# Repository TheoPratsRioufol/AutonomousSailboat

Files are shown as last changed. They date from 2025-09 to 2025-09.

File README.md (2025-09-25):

# An Autonomous Sailboat To Cross the Ocean

This GitHub repository presents the engineering of *Posidonie*, a 2-meter sailboat designed to compete in the [Microtransat challenge](https://www.microtransat.org/), which involves crossing the Atlantic Ocean autonomously.

plot
**Fig 1:** The CAD Model of the *Posidonie* monohull autonomous sailboat.

The Journey started with a 1.3-meter prototype, *Baleine*, from an RC M Class sailboat:

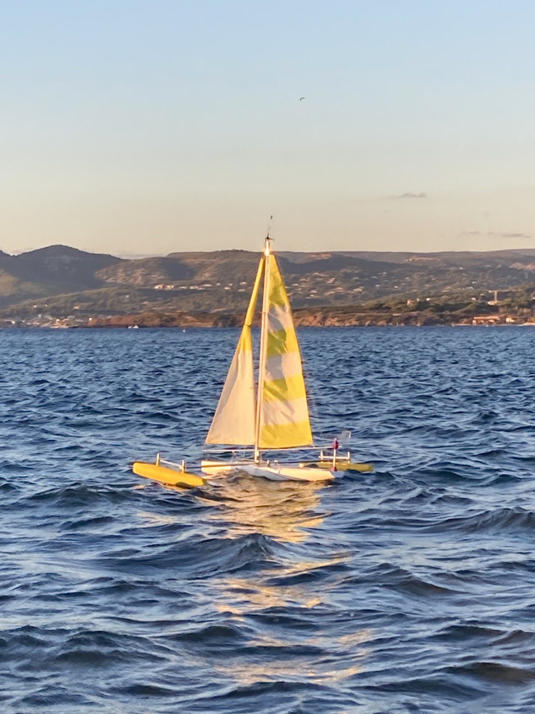
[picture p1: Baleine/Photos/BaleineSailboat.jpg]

**Fig 2:** The *Baleine* saiboat in a upwind course. You may notice the purple windvane at the back. The sail is controlled thanks to an electric winch.

This boat was used to test the control law, the fiberglassing process for the hull, and the architecture of the embedded electronics. 

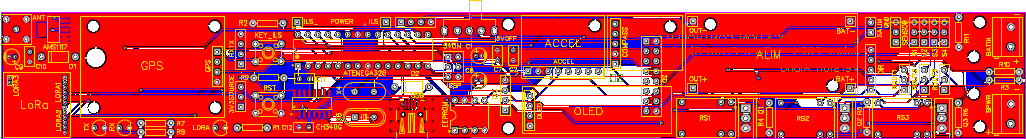
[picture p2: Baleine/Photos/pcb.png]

**Fig 3:** The *Baleine* main PCB. A LoRa module is used to communicate with a ground station. A GPS module and a magnetic compass provide the 6D position of the sailboat.

The promising results validated the global architecture. Meanwhile, the lack of upwind sailing performance ensured the need for a more precise design of the drift and sail area. This sizing is usually performed by a *Velocity Prediction Program* (VPP) program. As an open source VPP for this design was not available, a custom one has been developed:

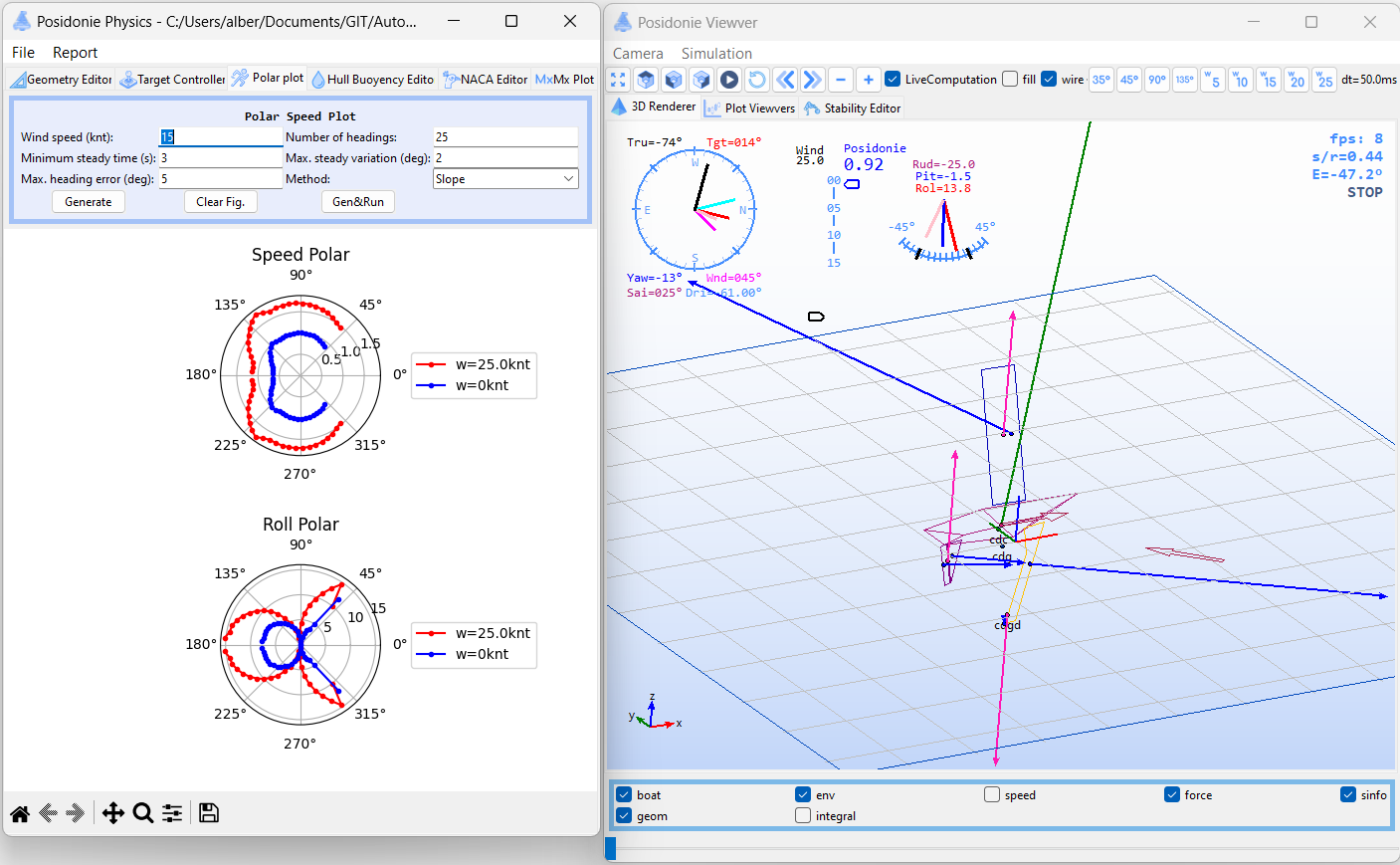
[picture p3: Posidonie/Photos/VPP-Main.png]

**Fig 4:** The *Velocity Prediction Program*. From CFD simulations of the Hull, Drift, and Rudder drag and lift, and according to the sail's control law and sail efficiency, different metrics of the sailboat are computed. (Here the polar plot - i.e., the velocity of the boat for different wind incidence)

The VPP program is fed from CDF Simulation of a NACA Profile under turbulent flow (for the drift, sail, and rudder) using COMSOL, and a hull drag profile in a free surface flow (Ansys Fluent).

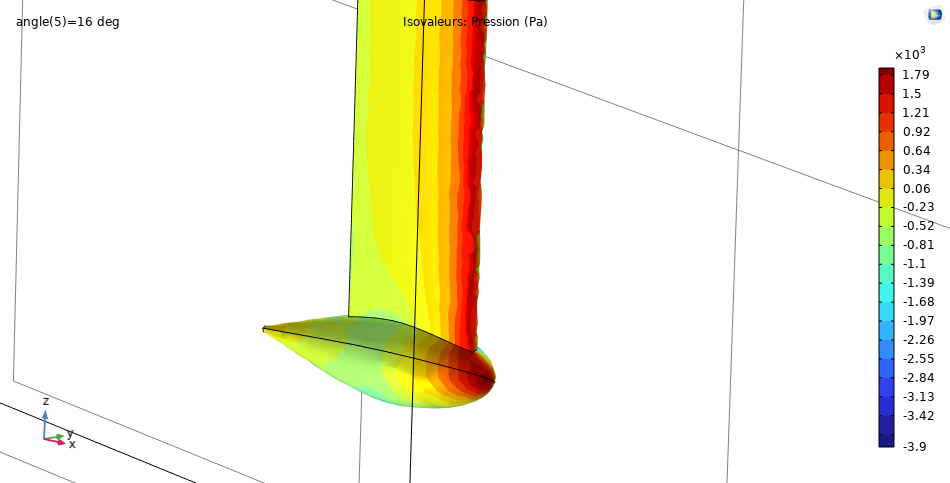
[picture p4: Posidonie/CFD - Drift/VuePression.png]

**Fig 5:** CFD Simulation of the keel's drag and lift as a function of the drift angle (usually around 4°).

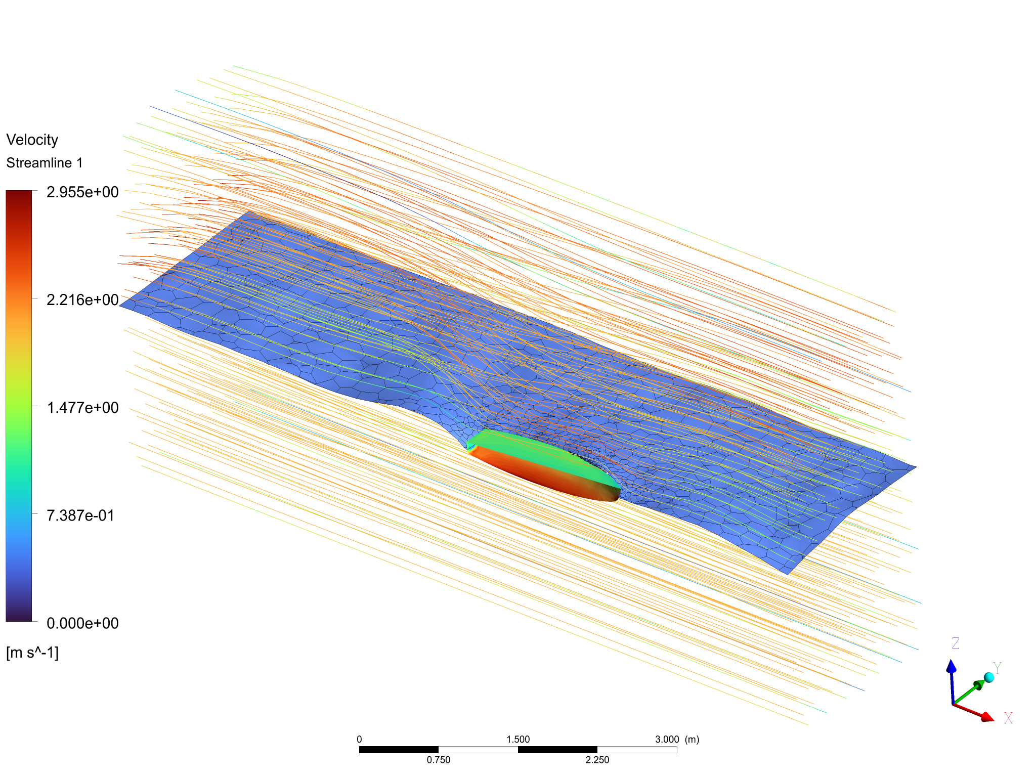
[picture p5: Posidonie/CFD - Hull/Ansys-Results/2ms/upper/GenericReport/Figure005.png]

**Fig 6:** CFD Simulation of the hull drag. As it is a displacement hull, the wave induced by the boat accounts for more than 60% of the overall drag.

To tackle the effect of waves on rotation movements and loads, a hydrodynamic refraction analysis was performed in Ansys AQWA. Past Weather forecast from the [Copernicus](https://www.copernicus.eu/fr) European model has been used in five typical zones (see Fig.7) to produce a statistical model of the wave's period and amplitude. The response of the hull for the most critical wave gave the location of the main beam of the boat's structure, located in the highest stress point (see Fig.8)

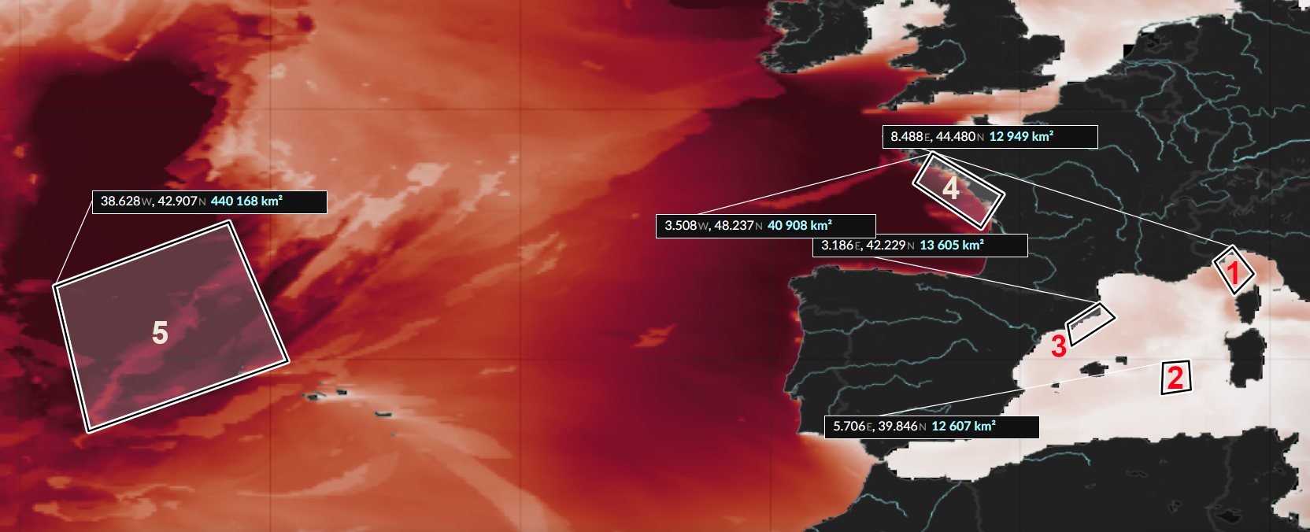
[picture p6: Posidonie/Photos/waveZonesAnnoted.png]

**Fig 7:** Zone considered to build a wave model. It turned out that all the waves created by the wind have similar characteristics. Only the swell greatly varies from each zone.

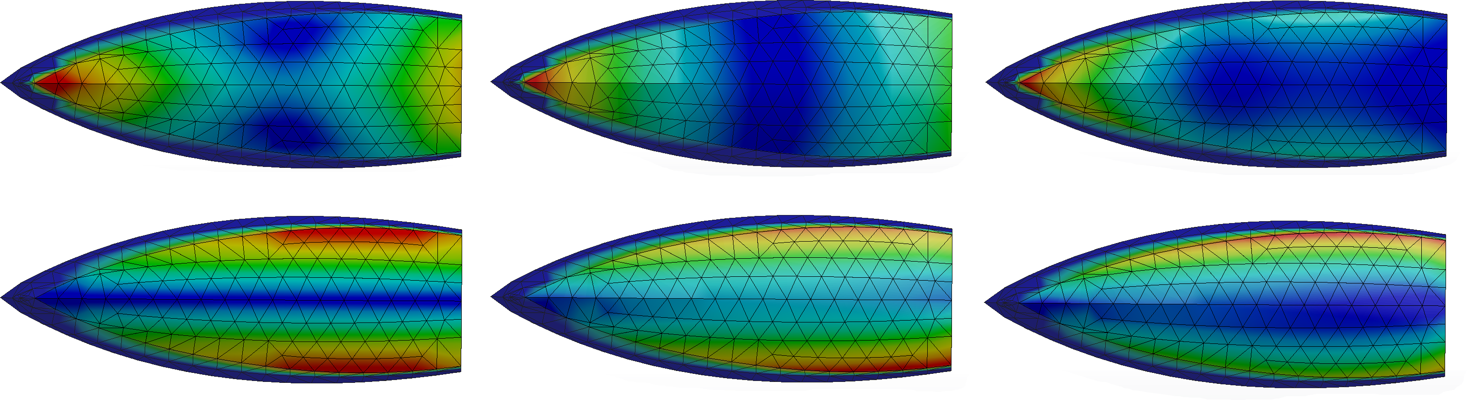
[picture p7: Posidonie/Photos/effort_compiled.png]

**Fig 8:** Location of the wave-hull mains pressure point, for the roll and pitch resonating frequency.

From the results of this main design step (sail surface, keel weight, and length...), a CAD model has been proposed (see Fig 1.). The physical implementation uses plywood and fiberglass as the main material. Prelemeray test of the plywood - fiberglass bound ensures a good mechanical strength of the boat:

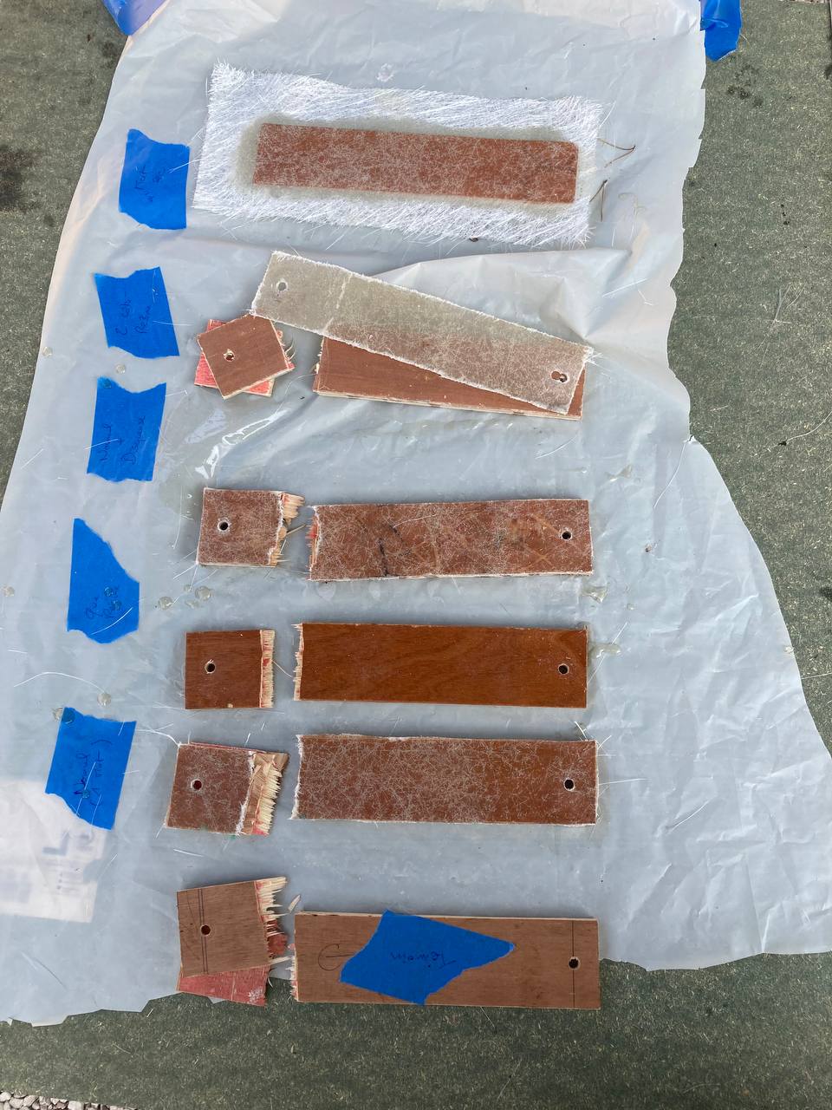
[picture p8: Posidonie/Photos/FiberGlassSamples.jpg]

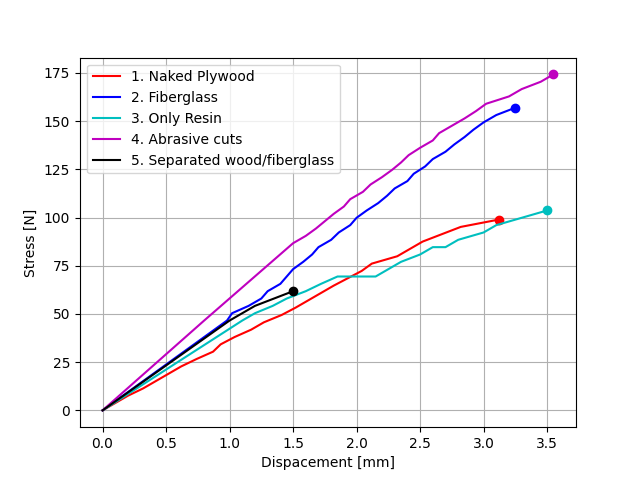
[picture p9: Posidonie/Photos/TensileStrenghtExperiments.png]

**Fig 9:** Sample of plywood-fiberglass composite for a strength analysis.

After countless hours, the hull is finally done!

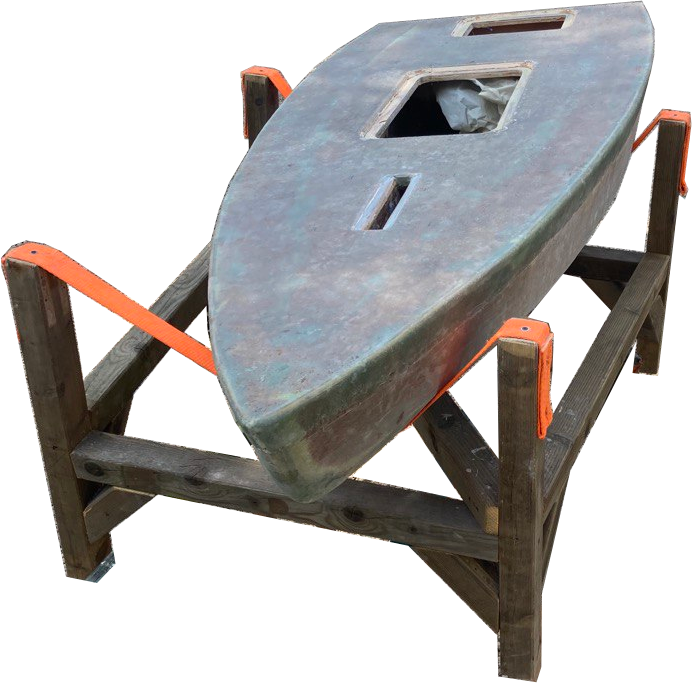
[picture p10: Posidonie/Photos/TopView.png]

**Fig 10:** The physicall hull before the Epoxy coating

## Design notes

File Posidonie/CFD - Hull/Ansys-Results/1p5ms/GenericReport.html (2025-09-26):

ANSYS Logo

Title

Generic Report

Date

2025/05/14 23:08:41

# Contents

Figure 1 Iso View of Wireframe
Figure 2 Iso View of Wireframe
Figure 3 Iso View of Wireframe
Figure 4 Iso View of Wireframe
Figure 5 Iso View of Wireframe
Figure 6 Iso View of Wireframe
Figure 7 Iso View of Wireframe
Figure 8 Iso View of Wireframe
1. User Data

Figure 1. Iso View of Wireframe

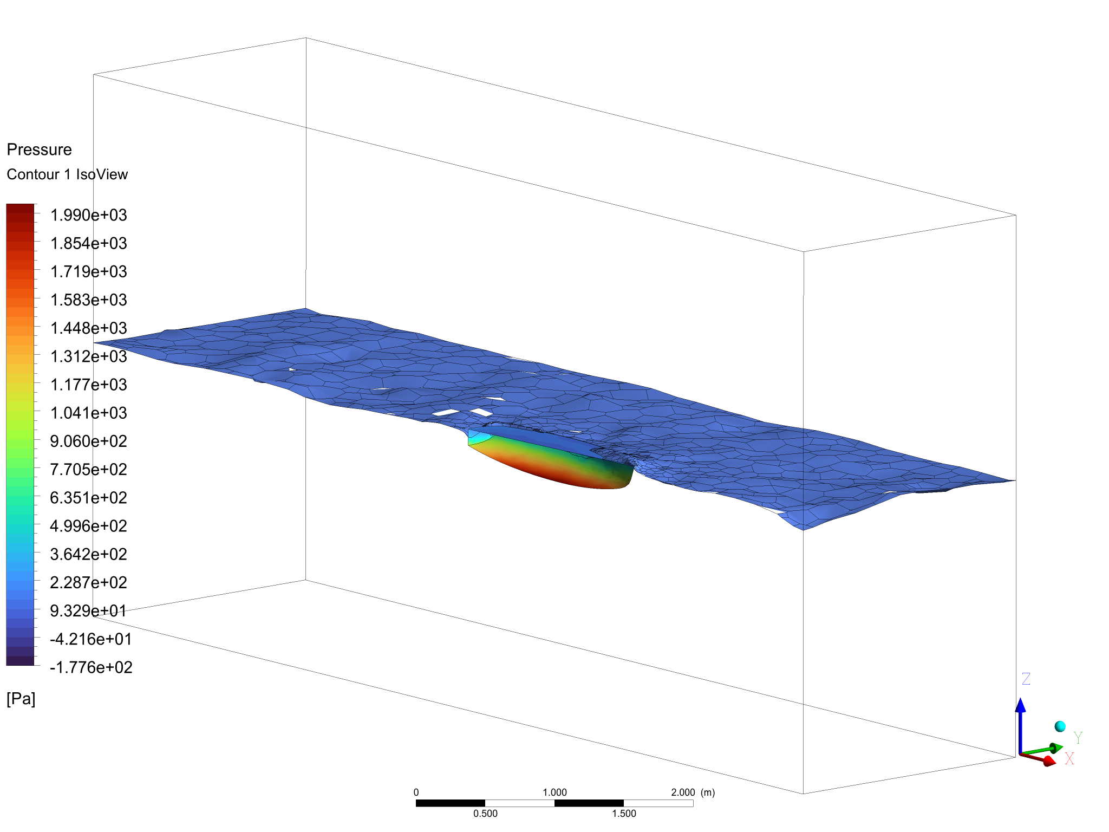
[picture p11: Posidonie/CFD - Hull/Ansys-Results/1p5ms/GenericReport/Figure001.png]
Figure 1 - GenericReport/Figure001.png


Figure 2. Iso View of Wireframe

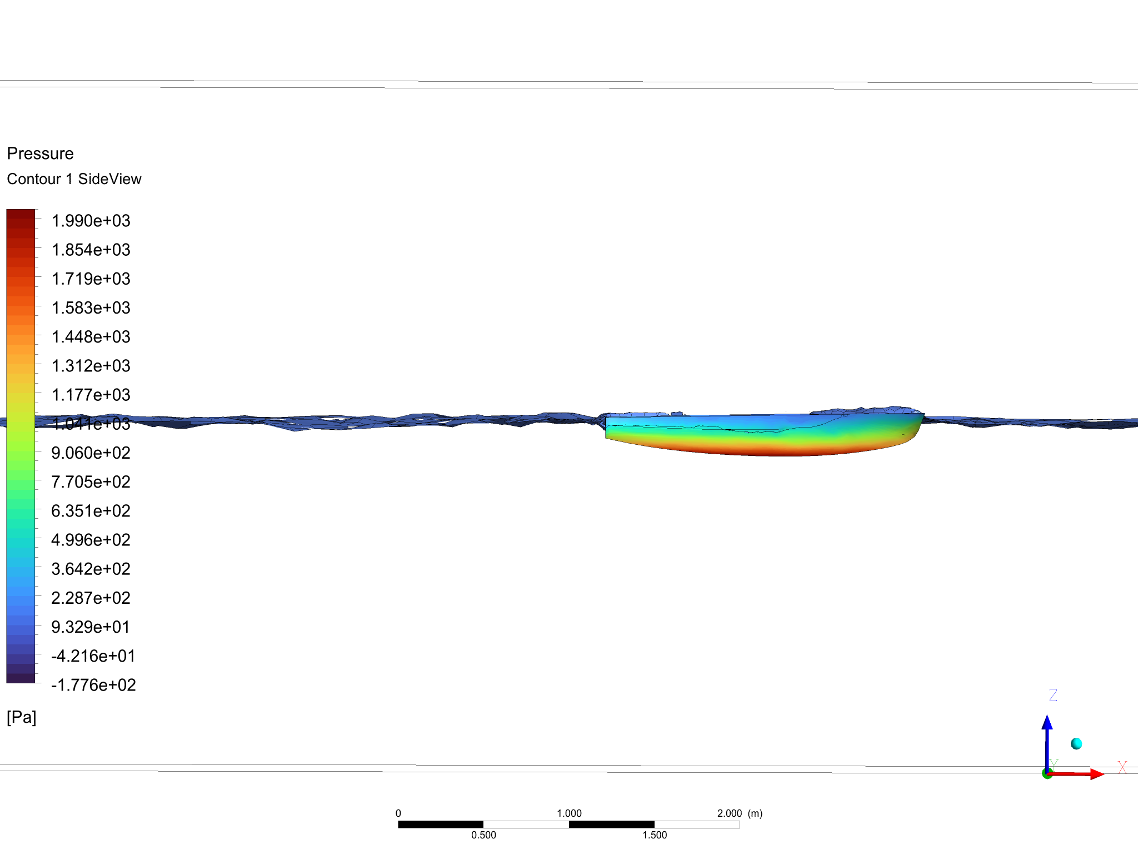
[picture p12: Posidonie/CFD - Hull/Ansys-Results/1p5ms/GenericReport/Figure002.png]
Figure 2 - GenericReport/Figure002.png


Figure 3. Iso View of Wireframe

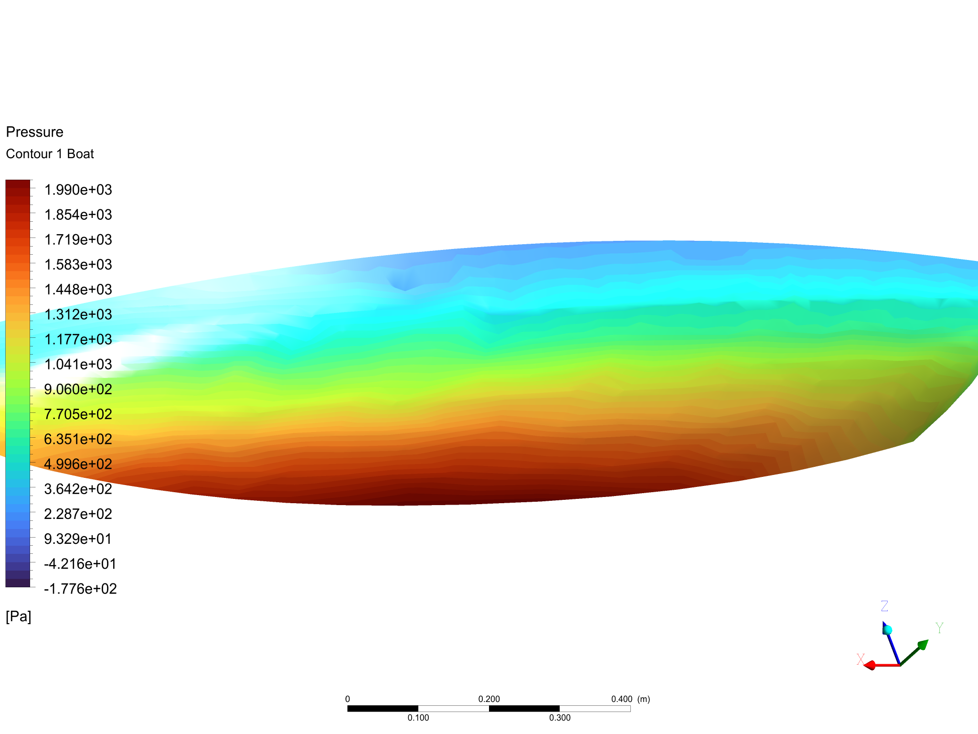
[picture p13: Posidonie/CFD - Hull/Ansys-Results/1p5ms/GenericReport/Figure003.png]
Figure 3 - GenericReport/Figure003.png


Figure 4. Iso View of Wireframe

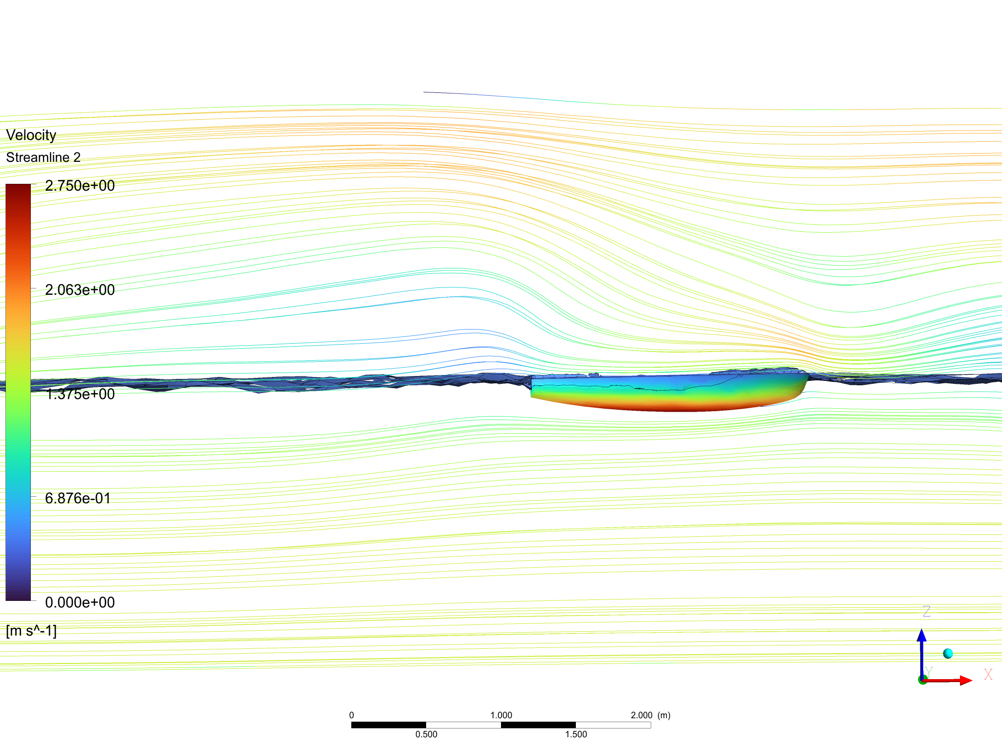
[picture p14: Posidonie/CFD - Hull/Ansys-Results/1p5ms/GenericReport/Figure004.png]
Figure 4 - GenericReport/Figure004.png


Figure 5. Iso View of Wireframe

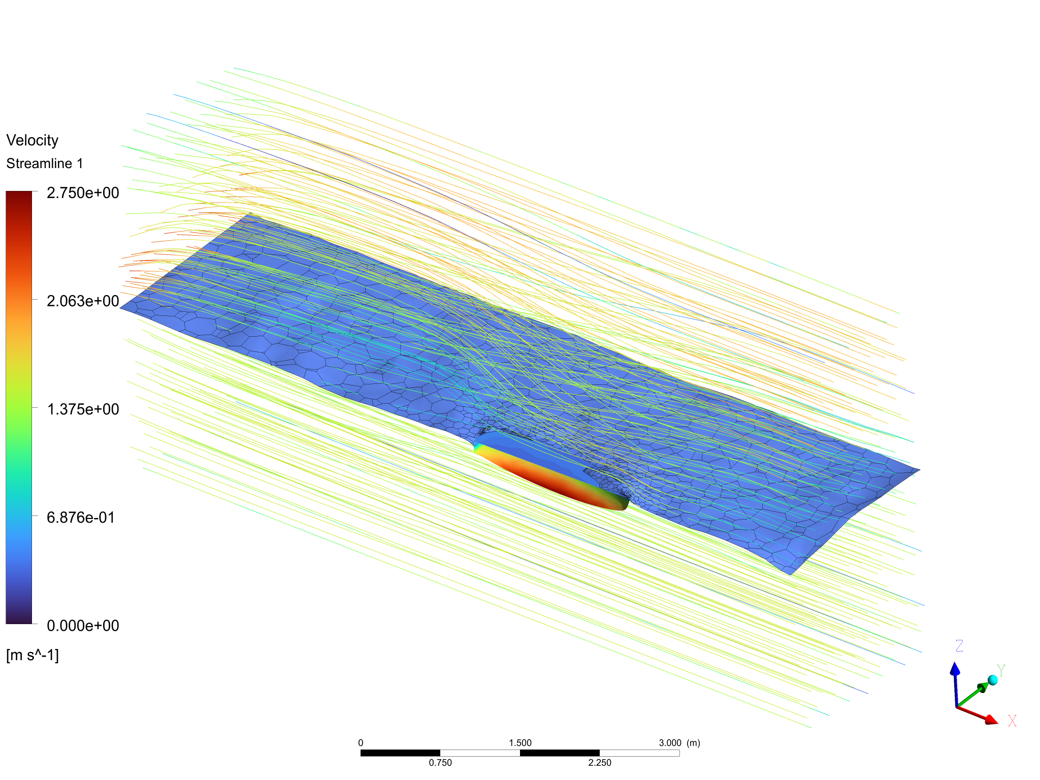
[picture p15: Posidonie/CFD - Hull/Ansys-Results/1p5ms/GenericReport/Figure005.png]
Figure 5 - GenericReport/Figure005.png


Figure 6. Iso View of Wireframe

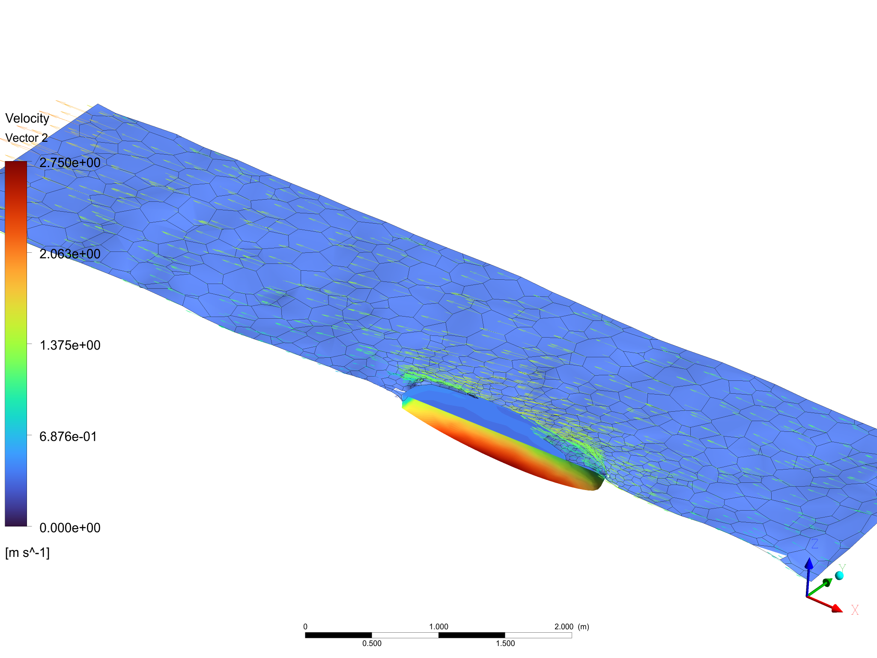
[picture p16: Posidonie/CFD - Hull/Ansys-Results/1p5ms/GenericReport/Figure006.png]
Figure 6 - GenericReport/Figure006.png


Figure 7. Iso View of Wireframe

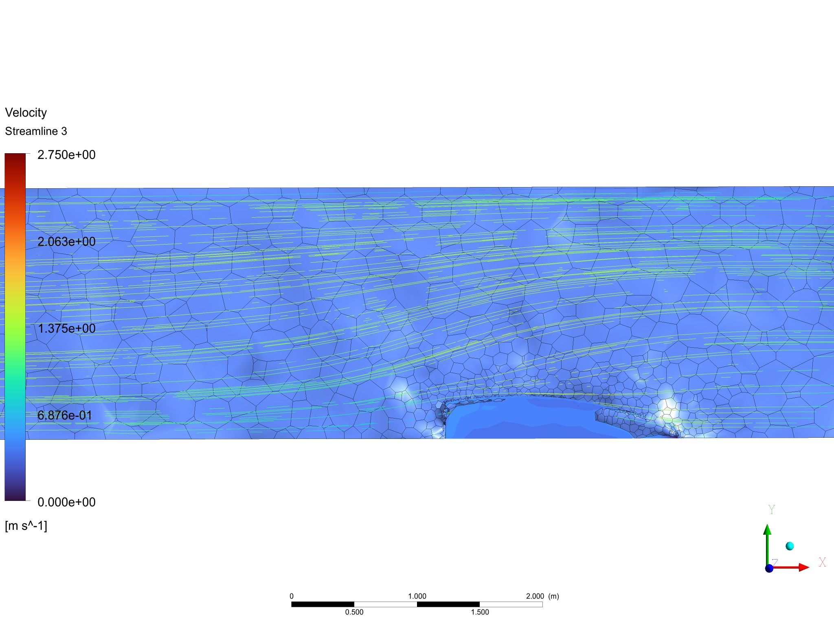
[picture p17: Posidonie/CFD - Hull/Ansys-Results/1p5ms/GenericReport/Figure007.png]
Figure 7 - GenericReport/Figure007.png


Figure 8. Iso View of Wireframe

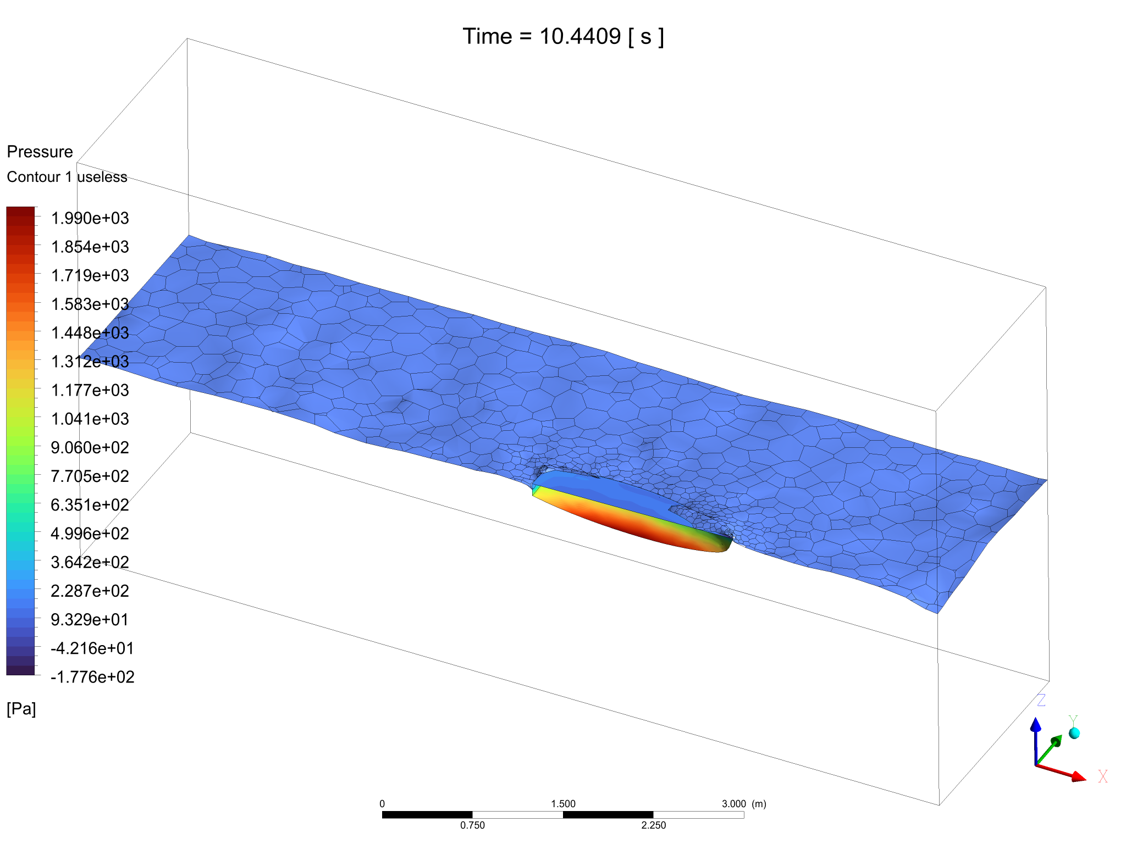
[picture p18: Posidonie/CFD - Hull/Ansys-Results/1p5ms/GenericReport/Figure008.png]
Figure 8 - GenericReport/Figure008.png


# 1. User Data

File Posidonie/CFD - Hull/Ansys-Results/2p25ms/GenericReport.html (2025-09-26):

ANSYS Logo

Title

Generic Report

Date

2025/05/15 01:05:22

# Contents

Figure 1 Iso View of Wireframe
Figure 2 Iso View of Wireframe
Figure 3 Iso View of Wireframe
Figure 4 Iso View of Wireframe
Figure 5 Iso View of Wireframe
Figure 6 Iso View of Wireframe
Figure 7 Iso View of Wireframe
Figure 8 Iso View of Wireframe
1. User Data

Figure 1. Iso View of Wireframe

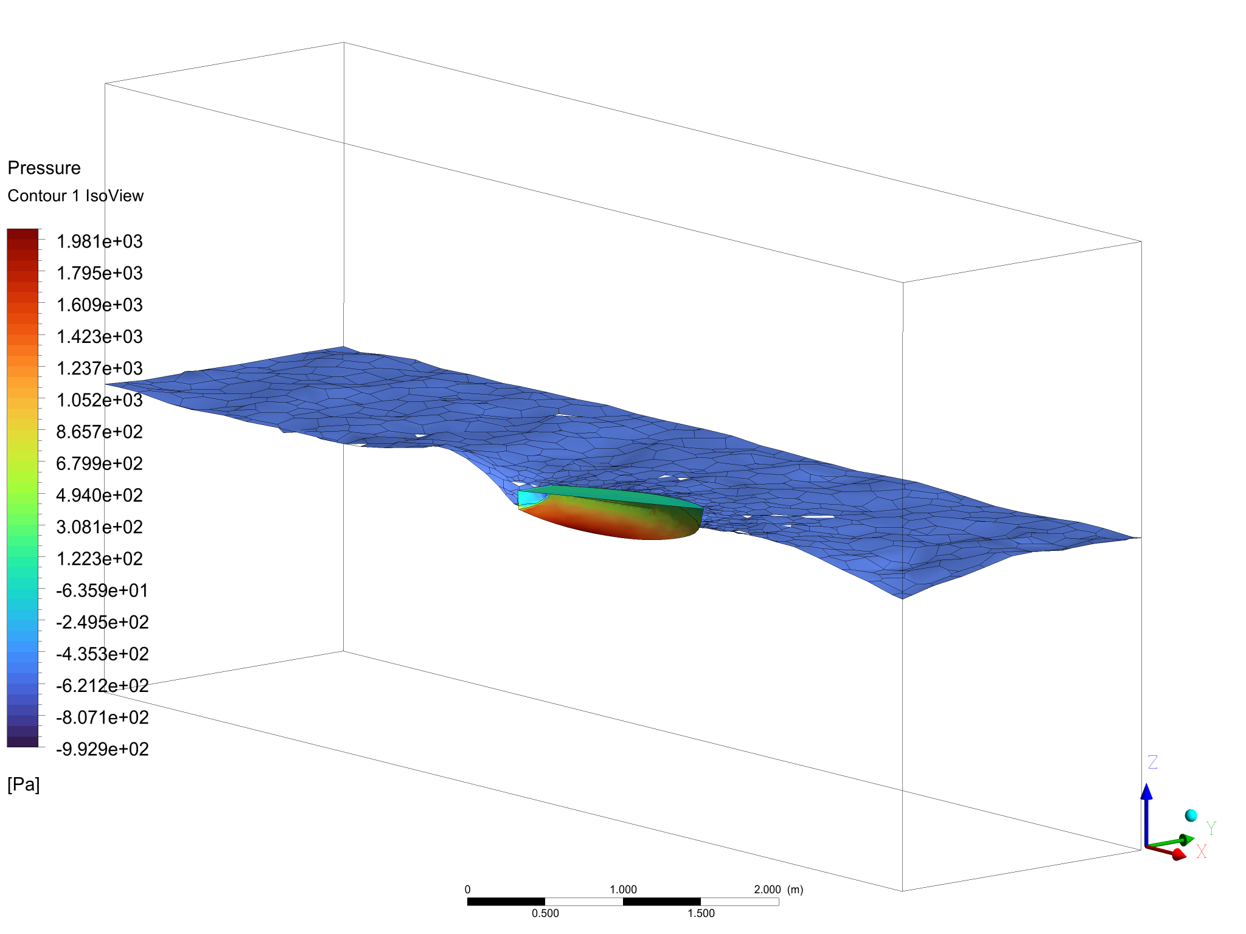
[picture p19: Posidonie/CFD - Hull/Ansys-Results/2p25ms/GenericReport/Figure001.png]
Figure 1 - GenericReport/Figure001.png


Figure 2. Iso View of Wireframe

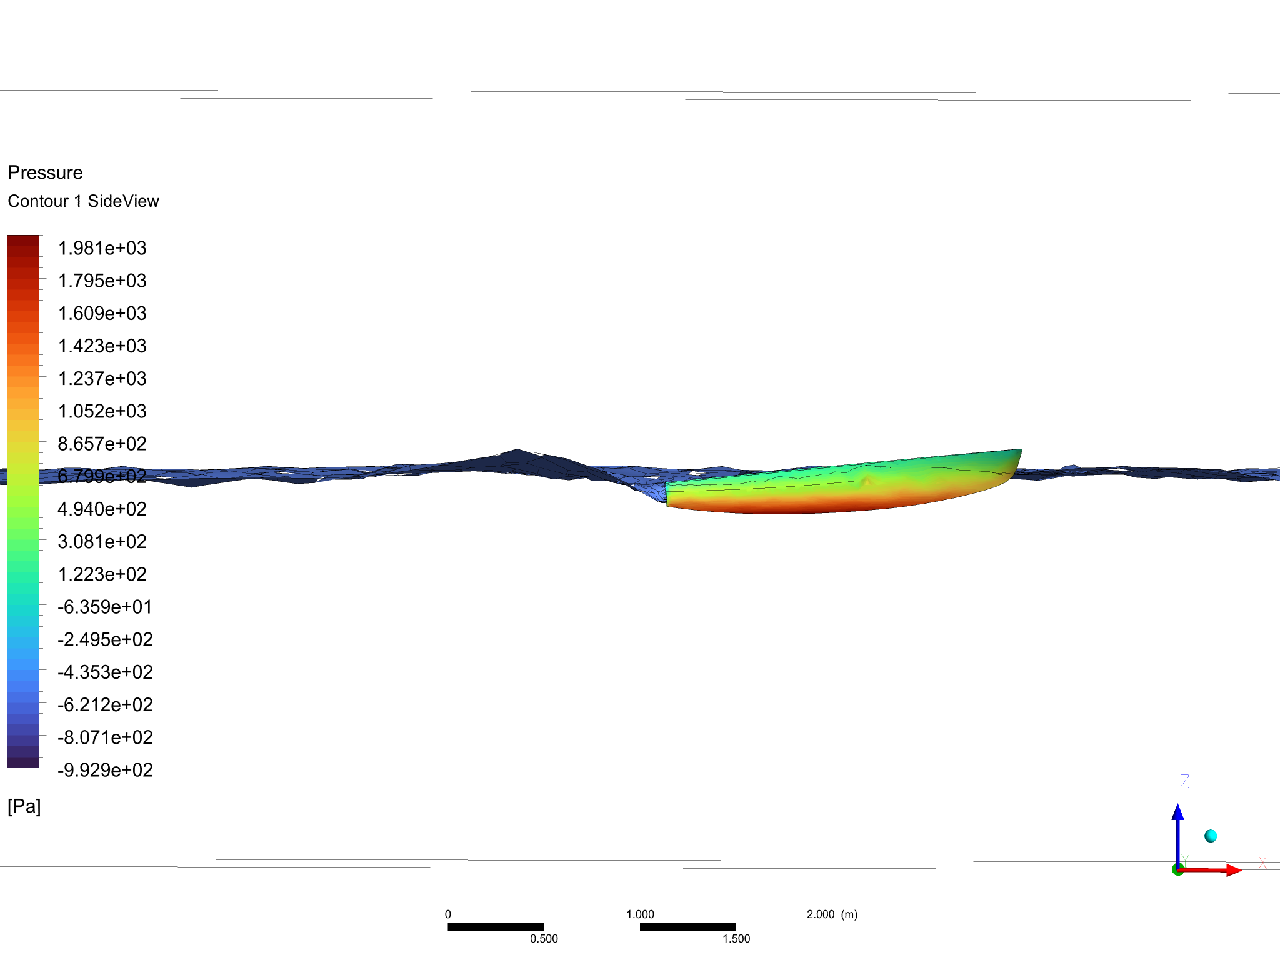
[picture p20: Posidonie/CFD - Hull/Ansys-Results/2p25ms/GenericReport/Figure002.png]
Figure 2 - GenericReport/Figure002.png


Figure 3. Iso View of Wireframe

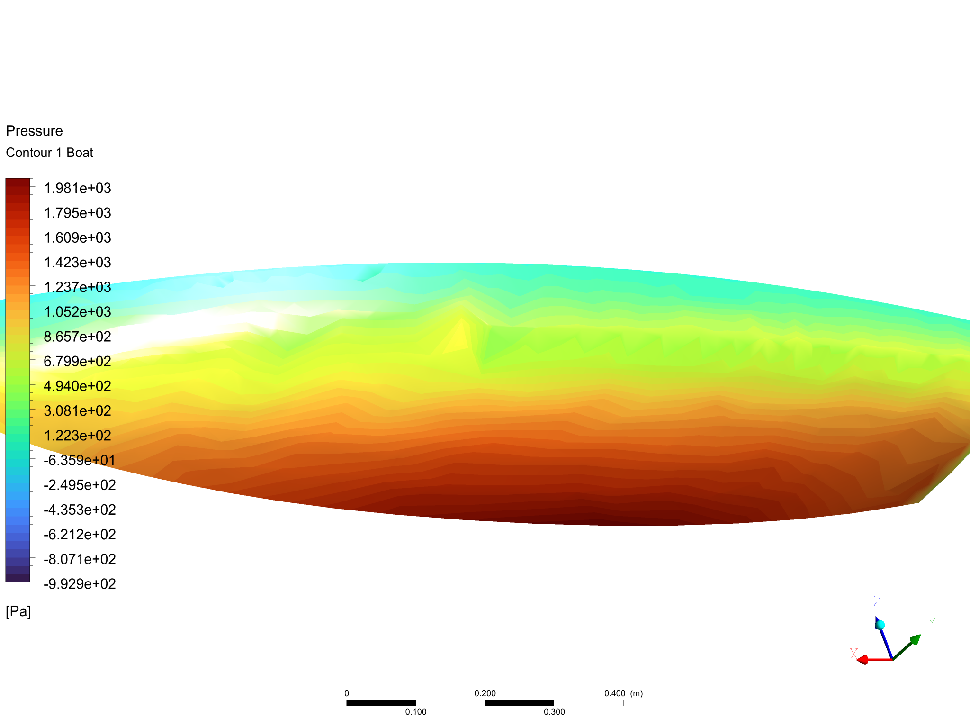
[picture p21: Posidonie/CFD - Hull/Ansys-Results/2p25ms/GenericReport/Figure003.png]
Figure 3 - GenericReport/Figure003.png


Figure 4. Iso View of Wireframe

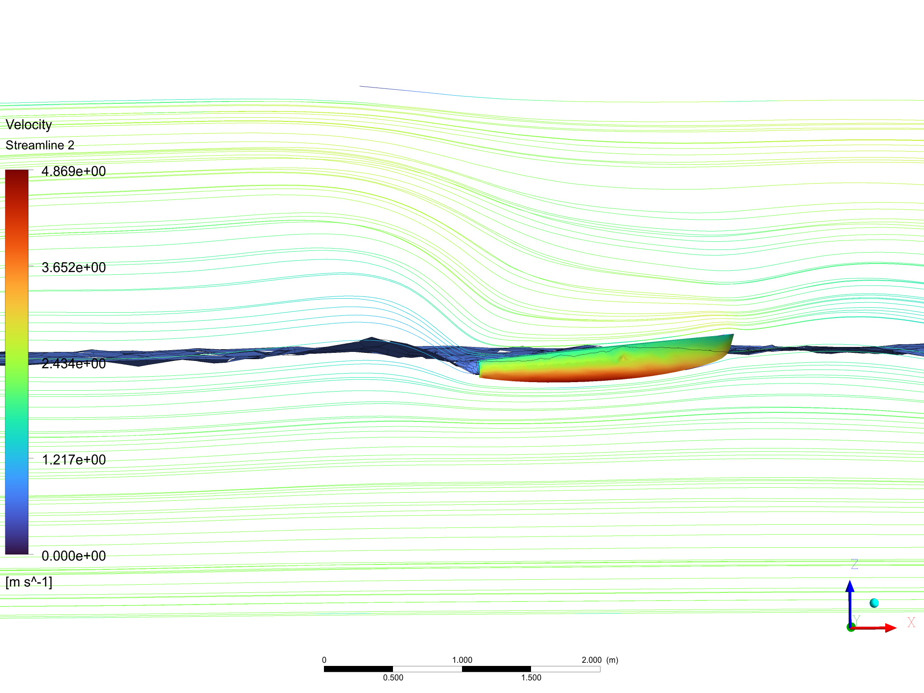
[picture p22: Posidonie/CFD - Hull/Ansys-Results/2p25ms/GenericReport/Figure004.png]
Figure 4 - GenericReport/Figure004.png


Figure 5. Iso View of Wireframe

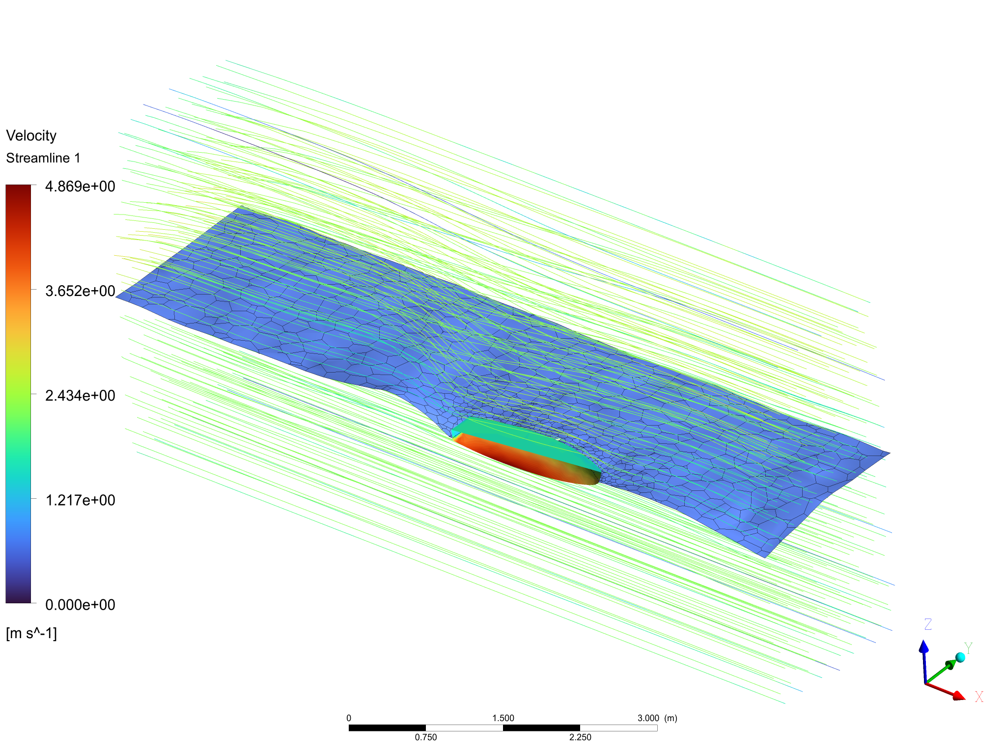
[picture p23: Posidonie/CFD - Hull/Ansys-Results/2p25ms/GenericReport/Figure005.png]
Figure 5 - GenericReport/Figure005.png


Figure 6. Iso View of Wireframe

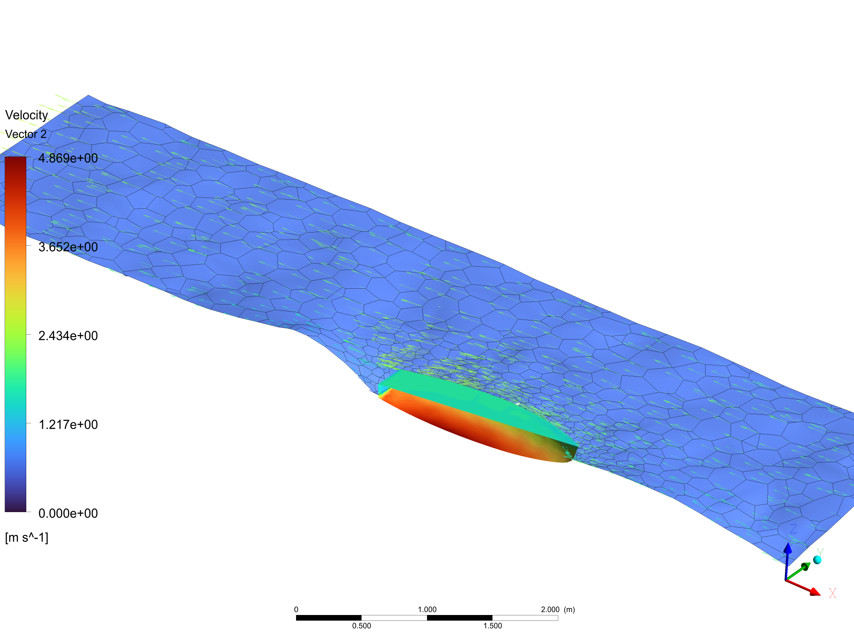
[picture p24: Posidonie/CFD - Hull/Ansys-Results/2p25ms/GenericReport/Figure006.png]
Figure 6 - GenericReport/Figure006.png


Figure 7. Iso View of Wireframe

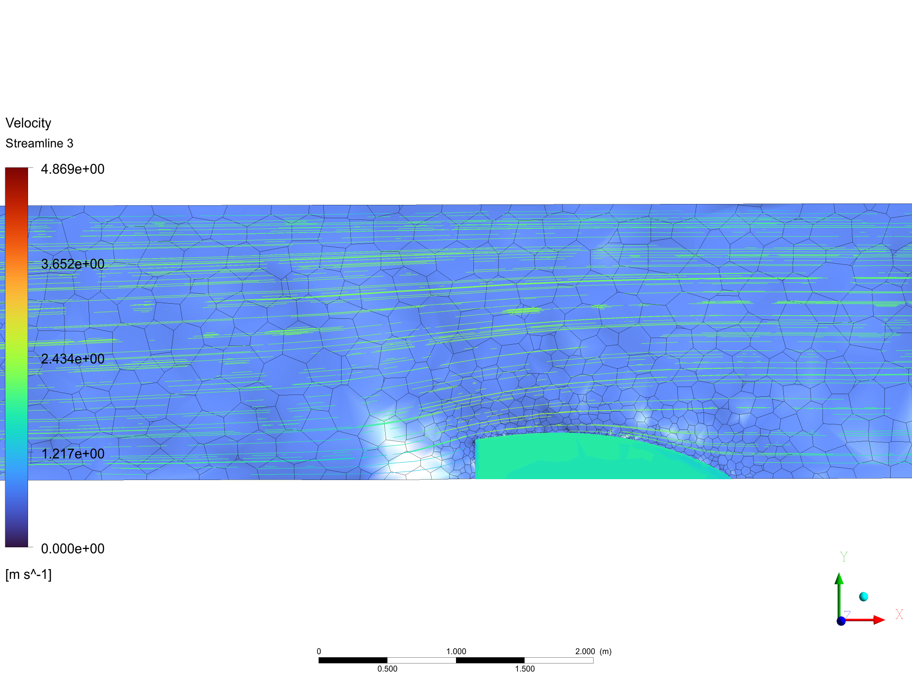
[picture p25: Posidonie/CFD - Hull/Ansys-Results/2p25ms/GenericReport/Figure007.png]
Figure 7 - GenericReport/Figure007.png


Figure 8. Iso View of Wireframe

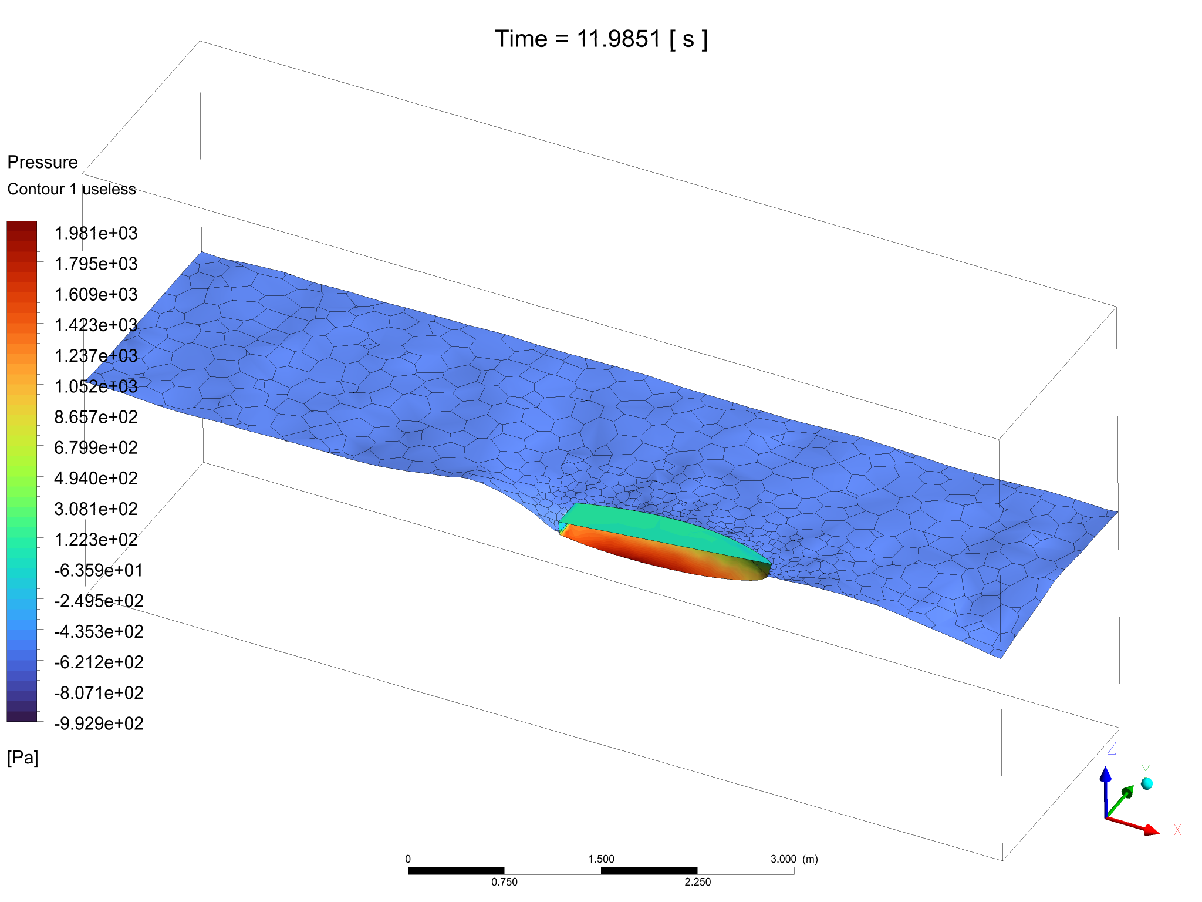
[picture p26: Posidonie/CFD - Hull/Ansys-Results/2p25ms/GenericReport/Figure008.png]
Figure 8 - GenericReport/Figure008.png


# 1. User Data

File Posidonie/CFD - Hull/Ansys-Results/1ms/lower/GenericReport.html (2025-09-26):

ANSYS Logo

Title

Generic Report

Date

2025/05/14 22:28:39

# Contents

Figure 1 Iso View of Wireframe
Figure 2 Iso View of Wireframe
Figure 3 Iso View of Wireframe
Figure 4 Iso View of Wireframe
Figure 5 Iso View of Wireframe
Figure 6 Iso View of Wireframe
Figure 7 Iso View of Wireframe
Figure 8 Iso View of Wireframe
1. User Data

Figure 1. Iso View of Wireframe

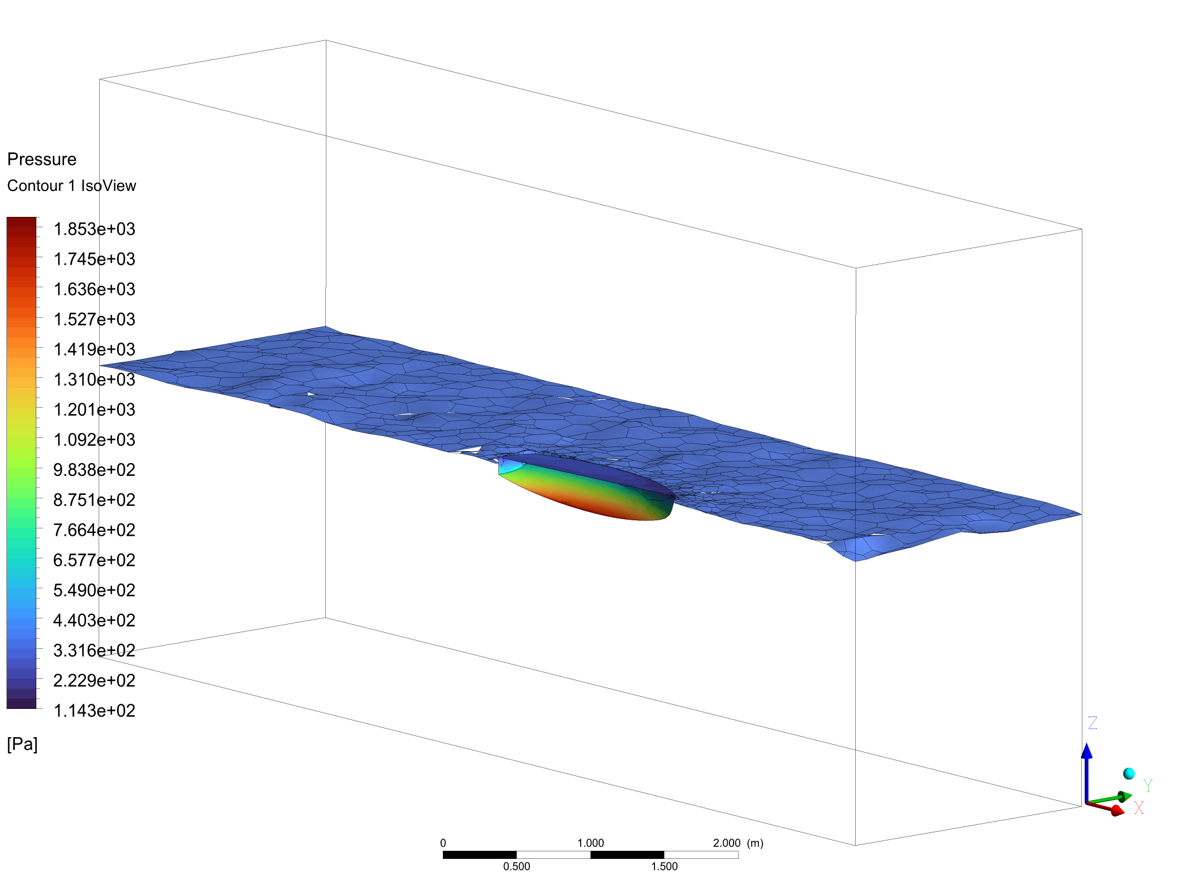
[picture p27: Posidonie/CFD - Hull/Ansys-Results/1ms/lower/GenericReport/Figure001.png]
Figure 1 - GenericReport/Figure001.png


Figure 2. Iso View of Wireframe

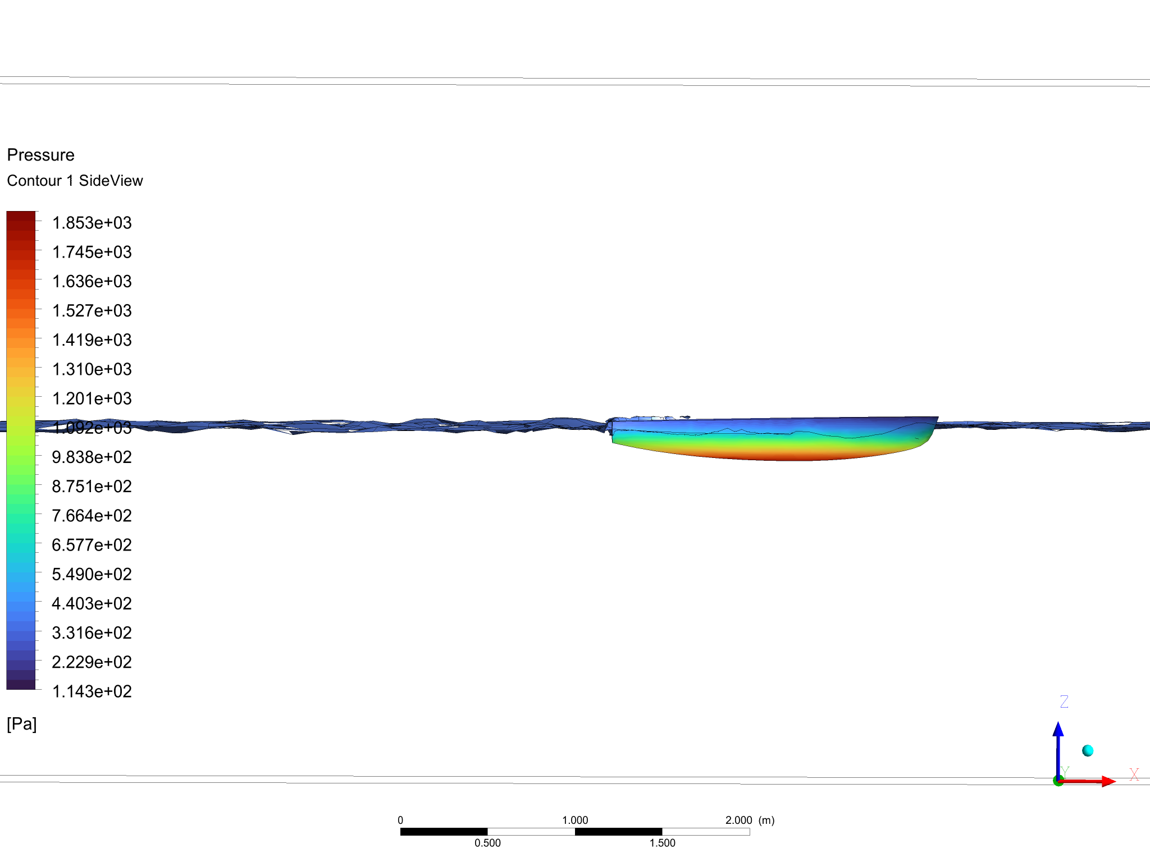
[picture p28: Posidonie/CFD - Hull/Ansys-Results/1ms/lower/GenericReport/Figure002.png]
Figure 2 - GenericReport/Figure002.png


Figure 3. Iso View of Wireframe

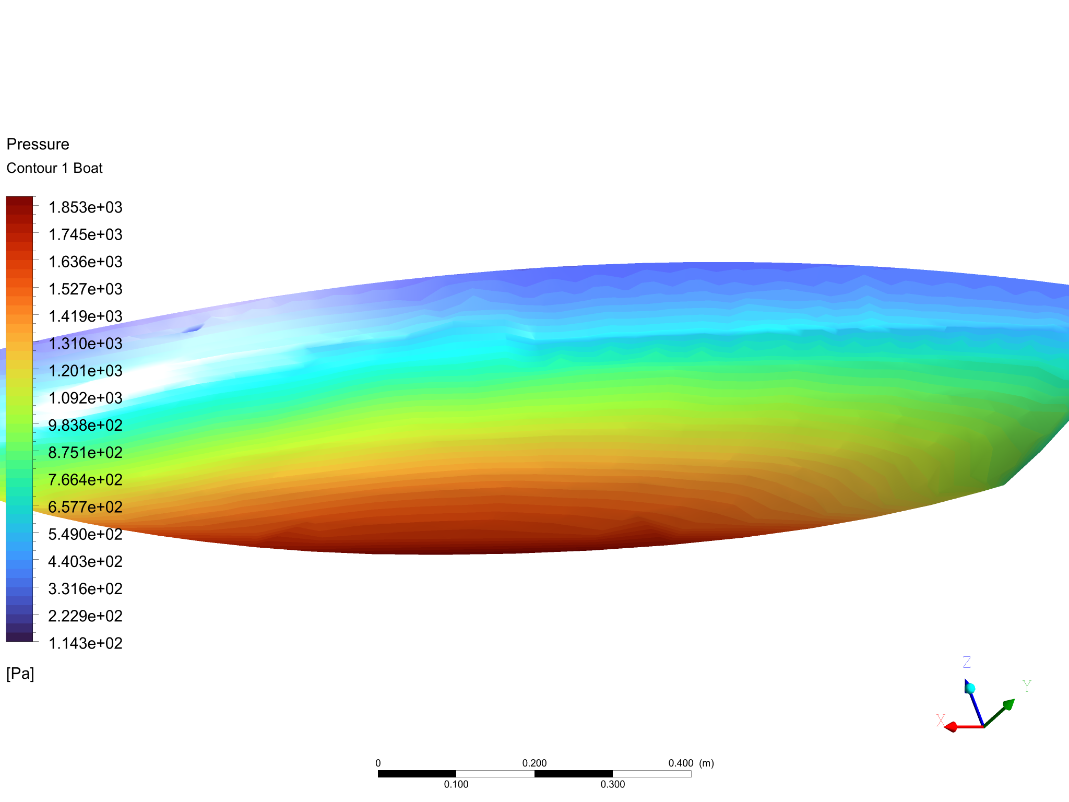
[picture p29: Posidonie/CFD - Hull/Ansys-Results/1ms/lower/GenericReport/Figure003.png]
Figure 3 - GenericReport/Figure003.png


Figure 4. Iso View of Wireframe

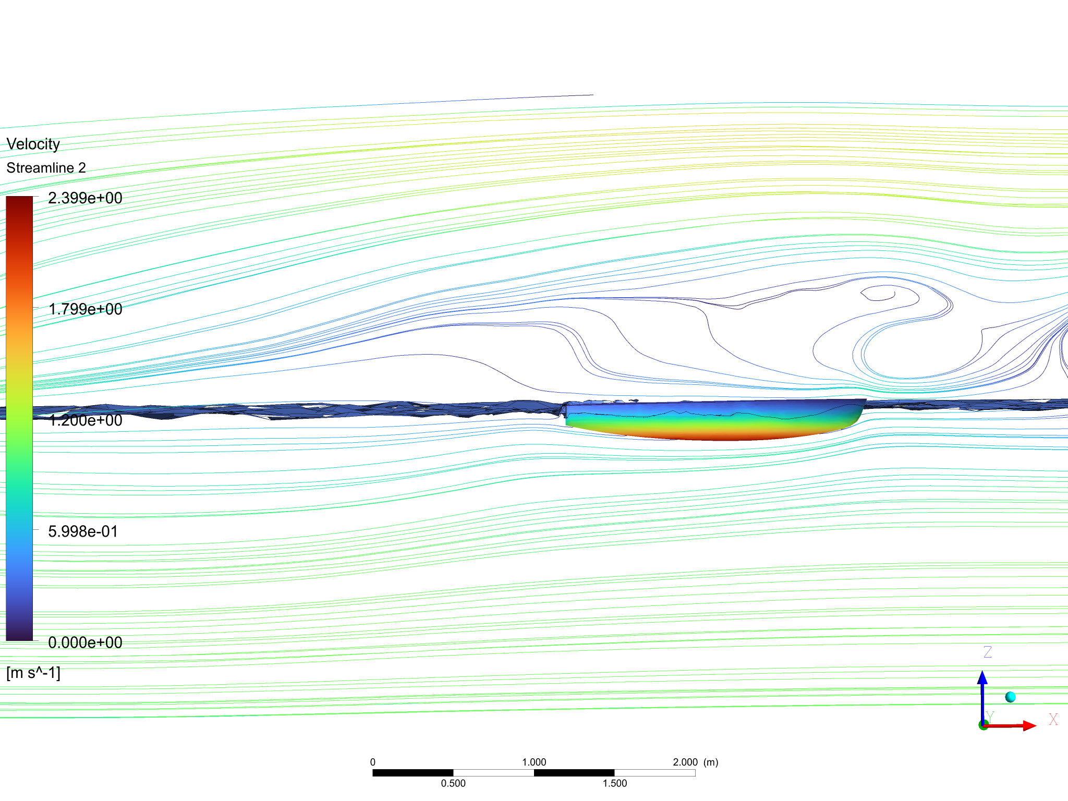
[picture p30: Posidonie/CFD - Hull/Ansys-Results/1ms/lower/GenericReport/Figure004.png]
Figure 4 - GenericReport/Figure004.png


Figure 5. Iso View of Wireframe

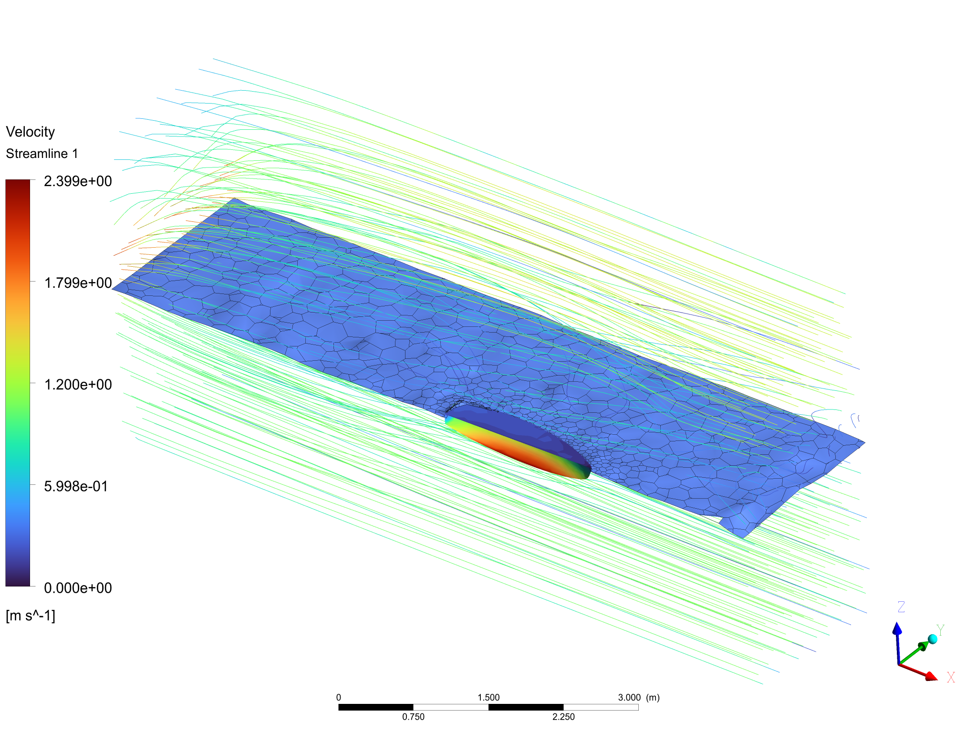
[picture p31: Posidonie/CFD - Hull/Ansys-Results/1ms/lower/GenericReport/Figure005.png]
Figure 5 - GenericReport/Figure005.png


Figure 6. Iso View of Wireframe

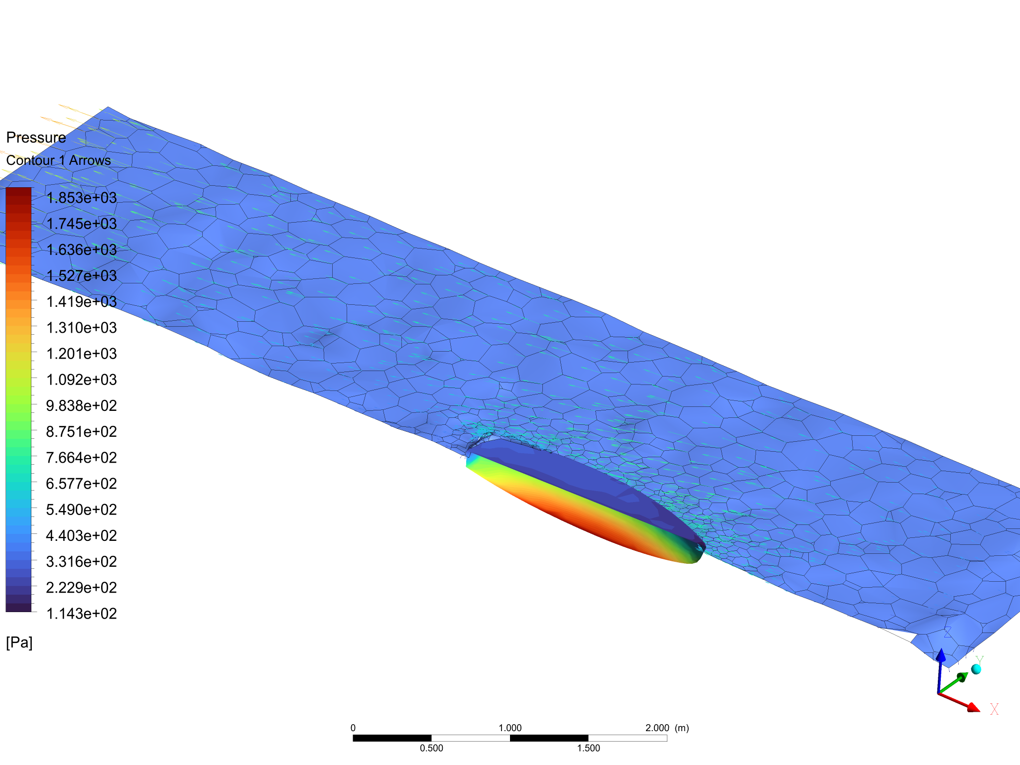
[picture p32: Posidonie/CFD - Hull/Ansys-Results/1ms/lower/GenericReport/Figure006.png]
Figure 6 - GenericReport/Figure006.png


Figure 7. Iso View of Wireframe

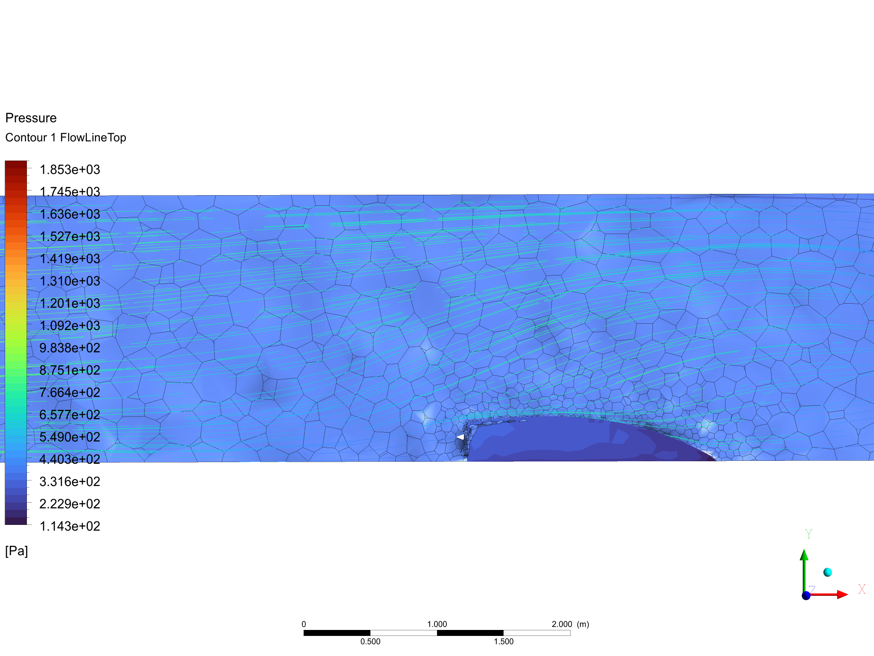
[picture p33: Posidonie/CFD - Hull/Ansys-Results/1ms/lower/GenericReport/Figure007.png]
Figure 7 - GenericReport/Figure007.png


Figure 8. Iso View of Wireframe

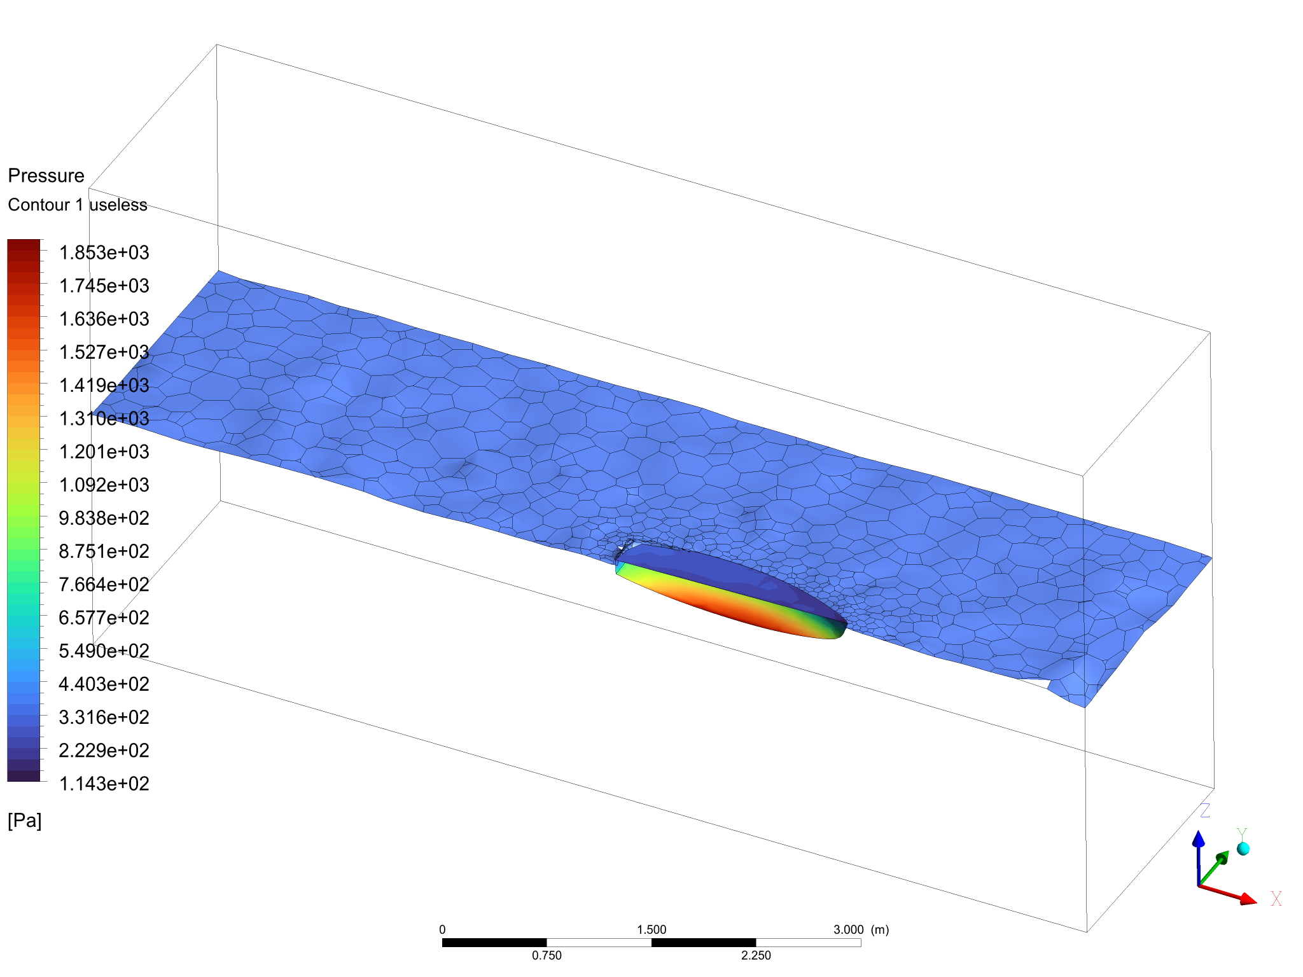
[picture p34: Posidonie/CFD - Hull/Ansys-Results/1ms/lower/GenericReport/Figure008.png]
Figure 8 - GenericReport/Figure008.png


# 1. User Data

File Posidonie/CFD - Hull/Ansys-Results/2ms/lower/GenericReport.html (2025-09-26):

ANSYS Logo

Title

Generic Report

Date

2025/05/14 21:36:45

# Contents

Figure 1 Iso View of Wireframe
Figure 2 Iso View of Wireframe
Figure 3 Iso View of Wireframe
Figure 4 Iso View of Wireframe
Figure 5 Iso View of Wireframe
Figure 6 Iso View of Wireframe
Figure 7 Iso View of Wireframe

Figure 1. Iso View of Wireframe

Figure 1 - GenericReport/Figure001.png

Figure 2. Iso View of Wireframe

Figure 2 - GenericReport/Figure002.png

Figure 3. Iso View of Wireframe

Figure 3 - GenericReport/Figure003.png

Figure 4. Iso View of Wireframe

Figure 4 - GenericReport/Figure004.png

Figure 5. Iso View of Wireframe

Figure 5 - GenericReport/Figure005.png

Figure 6. Iso View of Wireframe

Figure 6 - GenericReport/Figure006.png

Figure 7. Iso View of Wireframe

Figure 7 - GenericReport/Figure007.png

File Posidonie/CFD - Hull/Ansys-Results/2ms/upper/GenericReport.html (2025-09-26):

ANSYS Logo

Title

Generic Report

Date

2025/05/14 21:58:39

# Contents

Figure 1 Iso View of Wireframe
Figure 2 Iso View of Wireframe
Figure 3 Iso View of Wireframe
Figure 4 Iso View of Wireframe
Figure 5 Iso View of Wireframe
Figure 6 Iso View of Wireframe
Figure 7 Iso View of Wireframe
Figure 8 Iso View of Wireframe
1. User Data

Figure 1. Iso View of Wireframe

Figure 1 - GenericReport/Figure001.png

Figure 2. Iso View of Wireframe

Figure 2 - GenericReport/Figure002.png

Figure 3. Iso View of Wireframe

Figure 3 - GenericReport/Figure003.png

Figure 4. Iso View of Wireframe

Figure 4 - GenericReport/Figure004.png

Figure 5. Iso View of Wireframe

Figure 5 - GenericReport/Figure005.png

Figure 6. Iso View of Wireframe

Figure 6 - GenericReport/Figure006.png

Figure 7. Iso View of Wireframe

Figure 7 - GenericReport/Figure007.png

Figure 8. Iso View of Wireframe

Figure 8 - GenericReport/Figure008.png

# 1. User Data

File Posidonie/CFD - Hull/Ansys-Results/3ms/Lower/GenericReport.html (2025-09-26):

ANSYS Logo

Title

Generic Report

Date

2025/05/15 11:04:46

# Contents

Figure 1 Iso View of Wireframe
Figure 2 Iso View of Wireframe
Figure 3 Iso View of Wireframe
Figure 4 Iso View of Wireframe
Figure 5 Iso View of Wireframe
Figure 6 Iso View of Wireframe
Figure 7 Iso View of Wireframe
Figure 8 Iso View of Wireframe
1. User Data

Figure 1. Iso View of Wireframe

Figure 1 - GenericReport/Figure001.png

Figure 2. Iso View of Wireframe

Figure 2 - GenericReport/Figure002.png

Figure 3. Iso View of Wireframe

Figure 3 - GenericReport/Figure003.png

Figure 4. Iso View of Wireframe

Figure 4 - GenericReport/Figure004.png

Figure 5. Iso View of Wireframe

Figure 5 - GenericReport/Figure005.png

Figure 6. Iso View of Wireframe

Figure 6 - GenericReport/Figure006.png

Figure 7. Iso View of Wireframe

Figure 7 - GenericReport/Figure007.png

Figure 8. Iso View of Wireframe

Figure 8 - GenericReport/Figure008.png

# 1. User Data

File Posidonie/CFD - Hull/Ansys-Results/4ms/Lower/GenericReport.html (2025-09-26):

ANSYS Logo

Title

Generic Report

Date

2025/05/15 19:00:00

# Contents

Figure 1 Iso View of Wireframe
Figure 2 Iso View of Wireframe
Figure 3 Iso View of Wireframe
Figure 4 Iso View of Wireframe
Figure 5 Iso View of Wireframe
Figure 6 Iso View of Wireframe
Figure 7 Iso View of Wireframe
Figure 8 Iso View of Wireframe
1. User Data

Figure 1. Iso View of Wireframe

Figure 1 - GenericReport/Figure001.png

Figure 2. Iso View of Wireframe

Figure 2 - GenericReport/Figure002.png

Figure 3. Iso View of Wireframe

Figure 3 - GenericReport/Figure003.png

Figure 4. Iso View of Wireframe

Figure 4 - GenericReport/Figure004.png

Figure 5. Iso View of Wireframe

Figure 5 - GenericReport/Figure005.png

Figure 6. Iso View of Wireframe

Figure 6 - GenericReport/Figure006.png

Figure 7. Iso View of Wireframe

Figure 7 - GenericReport/Figure007.png

Figure 8. Iso View of Wireframe

Figure 8 - GenericReport/Figure008.png

# 1. User Data

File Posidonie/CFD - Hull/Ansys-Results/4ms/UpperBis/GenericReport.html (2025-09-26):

ANSYS Logo

Title

Generic Report

Date

2025/05/15 15:50:12

# Contents

Figure 1 Iso View of Wireframe
Figure 2 Iso View of Wireframe
Figure 3 Iso View of Wireframe
Figure 4 Iso View of Wireframe
Figure 5 Iso View of Wireframe
Figure 6 Iso View of Wireframe
Figure 7 Iso View of Wireframe
Figure 8 Iso View of Wireframe
1. User Data

Figure 1. Iso View of Wireframe

Figure 1 - GenericReport/Figure001.png

Figure 2. Iso View of Wireframe

Figure 2 - GenericReport/Figure002.png

Figure 3. Iso View of Wireframe

Figure 3 - GenericReport/Figure003.png

Figure 4. Iso View of Wireframe

Figure 4 - GenericReport/Figure004.png

Figure 5. Iso View of Wireframe

Figure 5 - GenericReport/Figure005.png

Figure 6. Iso View of Wireframe

Figure 6 - GenericReport/Figure006.png

Figure 7. Iso View of Wireframe

Figure 7 - GenericReport/Figure007.png

Figure 8. Iso View of Wireframe

Figure 8 - GenericReport/Figure008.png

# 1. User Data

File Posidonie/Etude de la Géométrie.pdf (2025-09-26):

# ETUDE MÉCANIQUE POUR LE DIMENTIONEMENT

# GÉOMÉTRIQUE DE Posidonie

Théo Prats Rioufol, Février 2025.

Résumé—Ce documment présente la mise en équation de la mécanique appliqué au projet Posidonie. A partir de ces équation et des contrainte du cahier des charges, un modèle de connaisance de Posidonie est proposé. Par l’étude de l’état stationaire et par l’emploie d’un algorithme d’optimisation, une méthode est proposé pour trouver les paramètre géométrique optimaux de Posidonie
Index Terms—Modélisation, Bateau Autonome, Optimisation, CDF, MMC, FEM.
I. PARAMÉTRAGE
A. Paramétrage géométrique


FIGURE 1. Schéma simplifié de l’ensemble de Posidonie. On distingue 4 ensembles mécaniques : dri ft (d), hull (h), sail (s) et rudder (r). Le référentiel attaché au bateau Rb est sittué au point B, où le plan (B,zb, xb) est un plan de symétrie. On nottera que xb est orienté dans le sens de la marche.

Pour commencer l’étude, la figure I-A présente les 4 ensembles principaux considéré pour segmenter la partie mécanique de Posidonie. Ces quatres éléments sont :
— La coque hull, notée (h). Le référentiel local du bateau (xb, yb,zb) est attaché en B, point de rotation du bateau. Le bateau est orienté dans le sens des xb croissants et le plan (B,zb, xb) définit un plan de symétrie longitudinal. — La voile sail, notée (s). L’origine du référentiel local de la voile Rs se sittue en S, au niveau du pied de mat. Le centre de poussée des forces aérodynamique exercé sur la voile est positioné sur l’axe du mat (pas de moment sur le mat selon zb).
— La dérive dri ft, notée (d). L’origine D du repère local de la dérive Rd, est sittué à l’extrème avant de cet ensemble.

— Le système safran, rudder, (safran et protège safran), noté (r). L’origine du repère local R, au niveau de l’axe de rotation de cet organe, est choisit pour s’aligner avec les forces hydrodynamique du safran (pas de moment selon zb)
Par la suite on notera Gi

,i ∈ {h,s,d,r} la coordonné du centre de gravité de l’ensemble i, i ∈ {H,S,D,R} l’origine de son repère local et Bi

,i ∈ {h,s,d,r} la coordonné du centre de carène de l’ensemble i. La base des repères des 4 sous ensemble est identique à Bb (les repère locaux sont exclusivement des translations).
Chaque ensemble possède son propre dimmentionement géométrique. La figure I-A présente le dimmentionement des ensembles s,d et r.
ld | dd
| γd
hd

dr

γa

lpr | lr

γr

hr

ls

γa

Ss,min

Ss,max

lms

ds

hs

FIGURE 2. Dimentionement particulier de 3 sous ensemble.

On notera que la voile est ammovible et sa surface appartient à l’intervalle [Ss,min,Ss,max]. On note λ ∈ [0,1] le facteur qui quantifie le déploiement de la voile : S = λ(Ss,max −Ss,min) +

Ss,min.

B. Paramétrage cinématique
Pour étudier la cinématique du bateau, le système de paramétrage angulaire doit être explicité. Ainsi pour transiter de la base terrestre B0 à la base attaché au bateau Bb, les rotations suivante doivent être effectuées succesivement :
1) Rotation ψ d’axe z0 = z1 (Lacet) : B0 → B1
2) Rotation θ d’axe x1 = x2 (Roulie) : B1 → B2
3) Rotation φ d’axe z2 = zb (Tanguage) : B2 → Bb

Toute les rotation sont effectué autour du point de rotation B du bateau, qui est confondu avec le point d’origine du repère Rb du bateau (qui relie l’origine du repère terrestre R0 à l’avant du bateau).

x0

x1

y1

y0

θ

z0 = z1

Cap θ

y1

z1
z2

y2

φ

x1 = x2

Rouli φ

zb

z2

xb

x2

ψ

y2 = yb

Tanguage ψ
B0 → B1 | → | B2 | → | Bb

FIGURE 3. Changement du référentiel terrestre au référentiel du bateau en 3 rotations.

II. CAHIER DES CHARGES

A partir du cahier des charges fonctionnels, on peut déduire le sous cahier des charges concernant le dimentionnement mécanique de posidonie. Ces exigenres sont détaillé dans la Tab. II

Exigence | Niveau
∀(A,B) ∈ R 2 , en mer plate, sous un vent réel de vitesse wc la vitesse moyenne pour aller de A vers B est : v ≥ vc. | wc = 10nds vc = 4nds
Avec la surface de la voile égale à Smin, sous un vent wmax, la gite θ et le tangage φ doivent être inférieur à leur limites respectives : θmax,φmax | wmax = 60nds θmax = 30deg φmax = 10deg

Pour une voilure de surface S, Une rafale de +∆w provoque une gite et un tangage inférieur à θmax +∆θ ,φmax +∆φ respectivement

Le mat est suffisament avancé pour permettre l’instalation de panneaux solaires La gite du bateau tend à le faire loffer (CE et CLR)

Le bateau ne doit pas s’eméler dans un filet de pêche

TABLE I
CAHIER DES CHARGES MÉCANIQUE

III. MÉCANIQUE

On souhaite obtenir une équation de la dynamique du bateau. D’une part, elle nous permettera de vérifier qu’un ensemble de paramètre géométrique convient pour le cahier des charges (en évaluant à l’équilibre), et d’autre part, cette équation nous permettera de simuler le bateau et de déterminer une loi de commande initiale.
Dans un premier temps, nous somme intéréssé à la dynamique du bateau dans son ensemble, les efforts de liaison ne sont pas important à ce stade. Toutefois, ils seront pertinent lors de l’analyse structurelle. Par exemple, les inters efforts s/h sont cruciaux pour le dimentionnement du mat et du pieds de mat.
Ainsi, on isole l’ensemble Ω = {h,s,d,r}
On se place dans le référentiel terrestre R0 = (0,ux,uy,uz)

Pour passer du référentiel R0 galliléen, à celui du bateau Rb, il faut :
— Appliquer une translation par le vecteur OB.

— Appliquer les rotations sucessive de centre B : R(B0 → B1) = Rθ ,R(B1 → B2) = Rφ ,R(B2 → Bb) = Rψ
On en déduit donc la relation :

x|Rb = RψRφRθ ( x|R0 −OB
| {z }
x est amené en B

)

Où OB la position du bateau dans le repère R0. Par la suite, on pose R = RψRφRθ ,t = −R × OB. On notera que R est la matrice de passage de la base B0 vers la base Bb. On en déduit :

x|Rb = Rx|R0 +t

x|R0 = R

−1
(x|Rb −t)

Pour ce qui s’agit des vitesses, la relation de Varinion donne pour tout point A :

V(A ∈ Ω/R0) = V(B ∈ Ω/R0) +AB∧ωRb/R0

où ωR est le vecteur vitesse de rotation associé à R, V(xb ∈ Ω/R0) = VB la vitesse du point B par rapport au référentiel R0, c’est à dire celle du bateau.

A. Bilan des forces

Le bilan des forces est effectué sur chaque sous ensemble pour permettre de déduire l’ensemble des forces s’exercant sur Posidonie (Ω).
1) Force exercées sur h:
— Force de pesanteur Ph appliquée en Gh (centre de gravité de h).
— Poussée d’archimède Πh appliquée en Bh (centre de carène de h).
— Force de hydrodynamique Fhh appliquée en xHyd,h.
— Force de aérodynamique Fah appliquée en xaero,h.
— Force de liaison.
2) Force exercées sur d:
— Force de pesanteur Pd appliquée en Gd.
— Poussée d’archimède Πd appliquée en Bd.
— Force de hydrodynamique Fhh appliquée en xHyd,h. — Force de liaison.
3) Force exercées sur s:
— Force de pesanteur Ps appliquée en Gs
— Force de aérodynamique Fas appliquée en xaero,s .
— Force de liaison.
4) Force exercées sur r:
— Force de pesanteur Pr appliquée en Gr .
— Poussée d’archimède Πr appliquée en Br
— Force de hydrodynamique Fhr appliquée en xHyd,r
— Force de liaison (notamment due à la motorisation de direction !).
B. Détail des forces

Cette section présente le détails des expressions de chacune des forces identifiées précédemment. Les paramètre cinématique essentiels vont être mis en valeurs et la relation avec le dimentionement géométrique va être explicitée.

1) Force exercées sur h: Force de gravité et de flottaison

La coque ayant une forme complexe, la position du centre de gravité et de carène sont obtenu numériquement (voir figure III-B1). Notons toutefois que le centre de carène Bh dépend de l’orientation spatiale du bateau et de la masse de celui-ci Bh = Bh(φ,ψ,mb) où mb = mh + md + mb + ms est la masse totale du bateau. On remarquera que le paramètre θ n’intervient pas dans l’expression de BB(R) and la base Bb, due à la symétrie de révolution du plan d’eau selon l’axe zb. Bh,V(R) sont obtenus par calcul de l’intersection entre le bateau et le plan d’eau pour un ensemble de confi-
guration C = [−φmax,φmax] × [−ψmax,ψmax] × [−mmax,mmax],
puis les résultats sont linéarisés pour n’importe quel vecteur x = (φ,ψ,mb).

(h)

V(R)

Ωw

B

ψ

φ

θ

B(R)

Bb

B0

FIGURE 4. Calcul du centre de carène pour une rotation R. V(R) = Ω∩Ωw représente le volume d’eau déplacé par la coque, où Ωw est le demi volume z < 0 de l’eau.

On a donc :

Ph = −mhgz,Πh = V(R)ρwz

Bh(φ,ψ,mb)

où mh est la masse de la coque, et V(R) + Vr + Vd =

mb
ρw
(Hypothèse d’équilibre selon l’axe z). Leurs moments en B sont égaux à :

MB(Ph) = BGh ∧Ph,MB(Πh) = BBh ∧Πh

Pour estimer la masse de la coque, on remarque qu’elle est la somme des masses suivantes :
— Masse des parois de la coque mh,wall. On considère une masse surfacique ρhεh où εh est l’épaisseur de la coque et ρh la masse volumique du matérieux utilisé (par exemple, ρh = 1.19g/cm³ pour le plexiglass). On a

donc mh,wall = ρhεh
— Masse des équipements mh,equip : Panneaux solaire, moteur de barre, électronique, batterie...
— Masse des structures internes mh,struct. On les estimes comme étant une coupe longitudinale (de section Sl) et n coupe transversale (de section SL) : mh,struct = (Sl + nSL)εhρh avec Sl ≈ 0.8 × lhhh et SL ≈ 0.5 × lhLh (la coque est de longeur lh, de largeur Lh et de hauteur hh).

Force hydrodynamique

Ici également, la complexité géométrique de la coque nous impose à utiliser les résultats d’un solveur numérique. On simulera donc la force hydrodynamique Fhh exercée sur la coque grâce au logiciel Aqwa de Ansy. Cette force dépend de l’orientation du bateau dans le fluide (θ,φ,ψ), du vecteur vitesse du fluide par rapport au bateau −VB|Bb et du déplacement V(R). Par la suite, on se place dans des conditions "de croisière", sous l’hypothèse :

θ ≈ dθ,dθ ∈ [−2β,2β]

φ ≈ φ0 +dφ,dφ ∈ [−(φmax −φ0),φmax −φ0]

ψ ≈ ψ0 +dψ,dψ ∈ [−(ψmax −ψ0),ψmax −ψ0]

où ψ0,φ0 sont les angles du bateau quand il navigue au près (point de référence choisi). Ainsi, la formule de Taylor-Young nous donne :

Fhh(R,V(R),Vb) =Fhh(R0,V(R),Vb)

+

∂Fhh
∂ θ dθ +

∂Fhh
∂ φ dφ +

∂Fhh
∂ψ dψ

Avec R0 la rotation associé aux angles θ = 0,φ0,ψ0. Plusieurs simulation sont réalisées pour différentes vitesses VB, et on négligera l’effet de dV(R). Les simulations seront faites pour un déplacement moyen du bateau V(R). Pour estimer les dérivées partielles, on utilisera la méthode des différences finies avec h égal à la moitiée du demie intervalle du paramètre considéré. Le moment autour du point B est estimé de la même manière :

MB(Fhh) =MB(Fhh(R0,V(R),Vb))

+

∂MB(Fhh)
∂ θ dθ +

∂MB(Fhh)
∂ φ dφ +

∂MB(Fhh)
∂ψ dψ

Force aérodynamique

La force aérodynamique Fah exercée sur la coque dépend de la surface émergée de la coque. Toutefois, on fait l’hypothèse que la variation de la forme du volume émergé Veh face à un vecteur vitesse de vent apparent wa due au roulis et au tangague est négligable. Ainsi :

Fah = Fah(||wa||,θ)

Fah est obtenue par simulation numérique pour plusieurs points wa,θ ∈ [0,10]knt × [0,π], Fah.y étant impair en θ et Fah.h étant pair en θ.

2) Force exercées sur d: Force de gravité
Concernant la dérive, on suppose qu’elle est constitué d’une plaque (plate) trapézoidale d’un matériaux homogène, avec une quille (keel) (de masse suposée ponctuelle) fixée à son extrémitée. Ainsi :

xg,d =

xg,d,platemplate +xg,keelmkeel

mplate +mkeel

Pour un trapèze, on a :

xg,d,plate =

−(dd +ld)/2
0
−hd/2

Bd

,dd = hdtan(σd)

où Bd est le repère local de la dérive. La masse est estimé à l’aide de la masse volumique de la dérive ρd, et de son épaisseur εd :

mplate = Sdρdεd = ldhdρdεd

Quant-à la quille, elle se trouve au centre du bout de la dérive en Q (voir figure III-B2) :

xg,d,keel =

−(2dd +ld)/2
0
−hd

Bd

,dd = hdtan(σd)

La force de gravité est donc :

Pd = −(mplate +mkeel)guz

Force de flottaison
La quille, d’une masse mkeel, est réalisé dans un matériaux de masse volumique ρkeel. Ainsi, le volume de la quille est Vkeel = mkeel/ρkeel. Le volume de la plaque de la dérive est déduit par analyse géométrique : Vplate = Sdεd, d’ou la force d’archimède totale :

Πd = (Vplate +Vkeel)ρwguz

Le centre de carrène se déduit avec le barycentre des centres de gravité (qui sont aussi centre de carène des ensembles plate et keel) par les volumes :

xb,d =

xg,d,plateVplate +xg,keelVkeel

Vplate +Vkeel

Force hydrodynamique

dd | ld

hd

D

M(z)
A(z)

z

dF(z)

Q

v f(z)

dz

uzd

uxd

uyd

FIGURE 5. Paramétrage des forces hydrodynamique appliquées à la dérive

On suppose que la quille est constitué d’un profil NACA. On fait l’hypothèse forte de négliger les effets de bord (hd >> ld). Ainsi la force hydrodynamique totale Fhd de l’action du fluide sur la dérive est obtenue par intégration selon uzb de la force élémentaire linéique hydrodynamique dF(z) exercé sur la tranche dz de la dérive à l’altitude z :

Fhd =

Z 0

−hd

dF(z).dz

La force élémentaire dF(z) est exercée en M(z). On en déduit l’expression du moment de Fhb au point B :

MB(Fhd) = Z 0

−hd

(BM(z)∧dF(z) + MM(z)

(dF(z)))dz

où MM(z)

(dF(z)) est le moment de dF(z) calculé au point M(z). Le vecteur BM(z) est donné par :

BM(z) = BD+DA(z) +B(z)M(z) = BD+zu−ξ lduxd

u =

dd
hd
0
1

Bb
où ξ est la position longitudinale relative du centre de poussé. Notons que le vecteur de vitesse du fluide, opposé à celui du bateau, peu varier selon l’altitude z. Par exemple, un mouvement de rouli accélère la vitesse du fluide au bout de la dérive par rapport à sa base.

v f

α

ξ lp

FL

lp

M
FD

NACA XXXX

y

x

xp

yp

FIGURE 6. Simulation de mécanique des fluides pour obtenir la résultante hydrodynamique d’un profil NACA, pour différent angles d’incidence α

Pour calculer dF(z), on utilise une simulation de mécanique des fluides pour un profil p dans un repère Rp galliléen (de base Bp) centré sur le centre de poussé de ce profil M. La figure III-B2 détaille le paramétrage de cette simulation. On fait l’hypothèse que les forces hydrodynamiques s’écrivent de la manière suivante :

F = fDuxp + fLuyp =

1
2

CD(α)
CL(α)
0

Bp

ρSv²
f

où ρ est la masse volumique du fluide, vf sa vitesse et S la surface longitudinale du profil. Le coeficients CD et CL qui varient avec l’angle d’incidence α, sont obtenue en simulant le profil pour des valeurs de références ρ0, v0,S0,l0, pour un nombre de Reynold similaire à celui de la dérive dans un cas typique (vitesse de croisière par exemple). On a donc, pour un profil de largeur l, la force linéique qui s’exprime par :

dF(z) = 1
2

CD(α(z))
CL(α(z))
0

Bp

ρlv f(z)

2

En supposant ρ constant par rapport à z (eau supposée incompressible).

Déterminons à présent la valeur de l’angle d’incidence α(z) à l’altitude z. On note la vitesse du fluide par rapport à la section d’altitude z : V(f /p,z). Comme le fluide est immobile dans R0 (hypothèse d’abscence de courant marins), on en déduit :

V(f /p,z) = V(f ∈ R0,z)
| | {z | }
| =0

+V(R0/p,z)

V(f /p,z) = −V(p/R0,z) = −V(A(z) ∈ R/R0)

En applicant la formule de Varinion en B, on obtient :

−V(f /p,z) = V(B ∈ R/R0) +A(z)B∧ΩR/R0

−V(f /p,z) = VB
|{z}
| vitesse bateau

+ΩR/R0

∧(BD+zu)

On remarquera que pout un bateau à l’équilibre (ΩR/R0
), la
vitesse du fluide par rapport à la dérive est égale à l’opposée de celle du bateau ! L’angle d’incidence se calcule par sa définition :

cos(α(z)) = < v(f /p,z)|uxp > ||v(f /p,z)||

sin(α(z)) = < v(f /p,z)∧uxp|uzp > ||v(f /p,z)||

où < .|. > est le produit scalaire, et v(f /p,z) le vecteur vitesse du fluide par rapport à la section élémentaire à l’altitude
z. Notons qu’en D, on a α(xD.zb) = β où β est l’angle de dérive (voir figure III-B4).

Force de liaison

Pour cette étude, nous ne cherchons pas à les calculer.

3) Force exercées sur s: Force de pesanteur

xb

zb

ls

ξ ls

hs,min

hms

ds

hs(λ)

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
FIGURE 7. Paramétrage géométrique de l’ensemble (s). Le panneau semi transparent (1) coulise verticalement par rapport au reste de la voile (2)

La figure III-B4 précise le dimentionement géométrique de la voile coulissante (s). Un panneau (en rouge semi transparent) de hauteur he coulisse selon zb, par un paramètre λ ∈ [0,1]. Pour λ = 0, la hauteur de la voile hs(λ) est égale à hs,min = he + hms, tandis que λ = 1 donne hs = hms + 2he. Déterminons à présent la position du centre de gravité.
En faisant l’hypothèse que la voile est de masse volumique uniforme ρs

, la postion du centre de gravité G1,G1 des deux partie de la voile est confondu avec le centre géométrique. On a alors :

G2 = S+

(ξ −
1/2)ls
0
ds +

he+hms
2

Bb

G1 = S+

(ξ −
1/2)ls
0
ds + (λ +
1/2)he

Bb
Les masses des deux panneaux s’obtiennent par leur surface respective, et masse surfacique ρs
:

m1 = helsρs

,m2 = (he +hms)lsρs
,m2

Gs est finalement obtenue par la relation du baricentre, et la force de pesanteur Ps avec la somme des masses de (1) et (2) :

Gs =

G1m1 +G2m2
m1 +m2

Ps = −(m1 +m2)gz

Force aérodynamique

S
xb

yb

Rs

w wa αv

γs
| αs

αw

v

FL,s
FD,s

FIGURE 8. Détail des angles intervenant dans l’écoulement de l’air par rapport à Posidonie, et détail de la surface de contrôle.

On considère que le vent apparent créé par la rotation du bateau est de même ordre de grandeur que la variation du vent réel par des rafales. Ainsi, on considère que le vecteur vitesse du vent est uniforme le long de la voile. La force aérodynamique Fas exercé sur la voile, illustrée dans la figure III-B3 est donnée par la relation suivante :

Fas =

1
2

CD(αs)

CL(αs)
0

Bs

ρhs(λ)lsV(f /s)

2

car la voile est rectangulaire. Bs est la base attaché à la voile, obtenue par une rotation d’axe zb de la base Bb par un angle γs

. La matrice de passage P(Bs → Bb) est notée Rγs
. αs
est l’angle d’incidence du vent apparent par rapport à la voile. La vitesse du vent par rapport à la voile (vent apparent) est noté V(f /s). Elle est égale à :

−V(f /s) = −V(f ∈ R0)
| | {z | }
| Vent réel

+ V(s/R0)
| {z }
vitesse du bateau

−V(f /s) = −w+VB

On en déduit l’angle d’incidence du vent sur la voile, αs représenté dans la figure III-B3 :

αs = ang(V(f /s), xs) = ang(V(f /s)|Bb
,Rγs

xs)

Calculons à présent la position du centre d’effort M de Fas .
Par symétrie, M se situe au milieux de la voile selon zb, et à ξ ls du coté droit. Ainsi :

M = S+

0
0
ds +

hs(λ)
2

Bb
On obtient ainsi l’expression du moment de Fas en B :

MB(Fas) = BM ∧Fas

xb
Br

yb

γr

βr
cr

FL,d FL,r

FD,r
β

v

FD,d

FIGURE 9. Détail des angles intervenant dans l’écoulement de l’eau salée par rapport à Posidonie, et détail de la surface de contrôle.

4) Force exercées sur r: Force de flottaison et de pesanteur

dr

lpr

ξ lr | ξ lpr
lr

σr
G | M | hr
r | Gp

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
P(λ)

FIGURE 10. Paramétrage géométrique de l’ensemble (r) : protège safran (gauche) et safran (droite)

La figure III-B4 précise le dimentionement géométrique du safran et du protège safran. On suppose que le safran et le protège safran sont réalisé dans un matériaux de masse volumique ρr homogène. Ainsi, la position du centre de gravité, de flottaison, et géométrique sont confondu. On a donc :

Grud = Brud = R+

(

1
2 −ξ )lr
0
−

hr
2

Bb

Gp = Bp = R+

(1−ξ )lr +

lpr
3
0
−

hr
3

Bb
Les masses sont calculé à partir du volume de ces deux éléments d’épaisseur εr
:

Vpr =

lprhr
2

εr

,mpr = Vprρr

Vrud = lrhrεr

,mrud = Vrudρr

Puis en faisant le barycentre des forces de pesanteur, on obtient le centre de gravité de (r) :

Gr = Br =

Grudmrud +Gprmpr

mrud +mpr

Avec la force de flottaison Πr et de pesanteur Pr associées :

Pr = −(mrud +mpr)gz0,Πr = (Vrud +Vpr)ρwgz0

Force hydrodynamique - Safran

Commençons par calculer la force hydrodynamique appliqué sur la partie mobile de l’ensemble r. La figure III-B4 détaille le paramétrage du safran. On suppose que le safran est de forme rectangulaire de taille lr ×hr
. De plus, le safran étant de hauteur bien inférieur à celle de la dérive, on suppose que le vecteur vitesse du fluide est constant le long du safran. Ainsi, l’expression de la force hydrodynamique s’écrit :

Fhr =

1
2

CD(αr)

CL(αr)
0

Br

ρhr

lrV(f /r)

2

Fhr

|Bb =

1
2

Rγr

CD(αr)

CL(αr)
0

Br

ρhr

lrV(f /r)

2

où Br est la base attaché au safran et V(f /r) le vecteur vitesse du fluide par rapport au safran. On note P(Br → Bb) = Rγr la
matrice de changement de base de Br vers Bb issue de la rotation d’angle γr autour de zb. L’angle d’incidence αr du fluide pour une commande γr est égal à :

cos(α) = < v(f /r)|uxr >
||v(f /r)|| =

< v(f /r)|R

−1
γr

uxb >
||v(f /r)||

sin(α) =

< v(f /r)∧R

−1
γr

uxb|uzb >
| ||v(f /r)||

Concernant le vecteur vitesse, on le déduit par l’expression suivante :

−v(f /r) = v(R ∈ R/R0) = VB +ΩR/R0

∧BR

Finallement, le moment de la force hydrodynamique appliqué au safran en B, s’exprime par :

MB(Fhr) = BM ∧Fhr +MM(Fhr)

où M = R−

hr
2

zb est le point d’application de Fhr sur le safran, et MM(Fhr) ≈ 0 est le moment en ce point (supposé nul car M est sittué au centre de poussé du safran).

Force hydrodynamique - Protège safran

L’angle d’incidence αr pour le protège safran est le même que celui du safran pour une commande nulle γr = 0. La force hydrodynamique Rhp exercé sur le protège safran (p) s’obtient par intégration sur la direction −zb, de la force élémentaire hydrodynamique sur une section de longeur l(z) = zlpr
hr

:

Fhp =

# Z hr

0

1
2

CD(αr)

CL(αr)
0

Bb

ρl(z)V(f /r)

2
dz

Fhp =

1
2

CD(αr)

CL(αr)
0

Bb

ρV(f /r)

2
(

# Z hr

0

zlpr
hr

dz)

Fhp =

lprhr
4

CD(αr)

CL(αr)
0

Bb

ρV(f /r)

2

Par raisonement géométrique, Fhp étant linéaire avec la largeur de la section auquel elle est appliqué on en déduit que le point d’appication K de Fhp se situe sur la droite (d) de coefficient directeur k (droite qui joint tout les centre aérodynamique des section d’altitude z). On sait que K est sittué au niveau du barycentre des forces. On repère un point P(λ) de (d) par la coordonée curviligne λ qui mesure la distance entre un point P(λ) de (d) et l’origine D de (d). Par linéarité : ||dF(P(λ))|| =

λE−λ
λE

||dF(D)|| car ||dF(P(λE))|| = 0 (section de largeur nulle).

# Z λK

0

λE −λ
λE
||dF(D)||dλ | =|{z}
| barycentre

# Z λE

λK

λE −λ
λE

||dF(D)||dλ

# Z λK

0

(λE −λ)dλ =

# Z λE

λK

(λE −λ)dλ

# Z λK

0

2λdλ =

# Z λE

λK

2λdλ

λ

2
K = λ

2
E −λ

2
| K =⇒ λK =

λE
√
2
Par le paramétrage de (d), on transforme λK en coordonée cartésienne dans Rr
:

K = P(λK) = D+λKk,λEk.zb = hr =⇒ λE = 1

Avec :

k =

| ξ lpr hr
| 0

Bb
D’où :
K = D+

k
√
2
On en déduit l’expression du moment en B :

MB(Fhp) = BK ∧Fhp

C. Calcul des matrices d’inerties
Dans la section précédente, l’ensemble des moments des forces exercées sur le système ont été calculées en B. On cherche à présent à obtenir la matrice d’inertie de Ω en B. Ci dessous, on rappelle le théorème de Huygens pour déplacer la matrice d’inertie I

Ω0
G

d’un système Ω0 en son centre de gravité G vers un point O tel que OG = xGux +yGuy +zGuz :

I

Ω0
O =
A | −F | −E
−F | B | −D
−E | −D | C
| | {z | }

I

Ω0
G

=

A+m(y

2
G +z

2
G

) −(F +mxGyG) −(E +mxGzG)
−(F +mxGyG) B+m(x

2
G +z

2
G

) −(D+myGzG)
−(E +mxGzG) −(D+myGzG) C +m(x

2
G +y

2
G

)

| | {z | }
notée mI(OG)
Ainsi, on se contentera de calculer la matrice d’inertie des composants h,s,d,r à leur centre de gravité.
1) Matrice d’inertie de (s): On suppose que les deux ensembles coulissants de (s) Ω1,Ω2 (voir figure III-B3) sont de masse volumique homogène. Leur épaisseur est notée εs et on approxime le profil NACA-XXXX par un rectangle. On cherche donc l’expression de la matrice d’inertie d’un parallépipède rectangle creux noté ΩP.

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
FIGURE 11. Paramétrage géométrique d’un paralélipède creux

Pour calculer la matrice d’inertie de ΩP on somme 4 matrices d’inertie de chacun des côtés 1,2,3,4 de ΩP. Chaque coté est modélisé par un parallélipède plein de centre de gravité G de matrice d’inertie :

IG(a˜,b˜, c˜) =

m

12 (b˜2 +c˜
2
) | 0 | 0
0

m
12 (a˜
| 2 +c˜

2
) | 0
0 | 0 | m
| | 12 (a˜ 2 +b˜2
)

Bb
où ˜a est la dimention du parallélipède dans la direction x, b˜ dans la direction y et ˜c est associé à z. La masse m est égale à abc˜ ρ. Pour ΩP :

OG1 = −bux,m1 = 4aceρ

OG2 = −cuy,m2 = 4abeρ

OG3 = bux,m3 = m1

OG4 = cuy,m4 = m2

I

ΩP
O = I

1
O +I

2
O +I

3
O +I

4
O

= 2

m2c

2 | 0 | 0
0 | m1b
2 | 0
0 | 0 | m1b

2 +m2c

2

+ 2I

1
G1

(e,2c,2a) +2I

2
G2

(2b, e,2a)
| | {z | }
(1,3),(2,4) sont identiques par translation

=

2m2c

2 +

2m1
3

(c

2 +a

2

) + m2
6

(e

2 +4a

2
) | 0 | 0
0 | 2m1b

2 +

m1
6

(e

2 +4a

2

) + 2m2
3

(b

2 +a

2
) | 0
0 | 0 | 2m1b

2 +2m2c

2 +

m1
6

(e

2 +4c

2

) + m2
6

(4b

2 +e

2
)

= 4ρ

2abec² +

2ace
3

(c

2 +a

2

) + abe
6

(e

2 +4a

2
) | 0 | 0
0 | 2aceb² +

ace
6

(e

| 2 +4a

2

) + 2abe
3

(b

2 +a

2
) | 0
0 | 0 | 2aceb² +2abec² + ace
| | 6

(e

| | 2 +4c

2

) + abe
6

(4b

2 +e

2

= 4ρ

2aebc² +

ae
6

(4c

3 +4ca² +be² +4ba²
) | 0 | 0
0 | 2aecb² +

ae
6
| (ce² +4ca² +4b

3 +4ba²
) | 0
0 | 0 | ae(2cb² +2bc² ) + ae
| | 6 (ce² +4c

3 +4b

3 +be²
)

=

2
3

aeρ

12bc² +4c

3 +4ba² +4ca² +be² | 0 | 0
0 | 12cb² +4b
| 3 +4ca² +4ba² +ce² | 0
0 | 0 | 12cb² +12bc² +4c 3 +4b

3 +be² +ce²

= I

ΩP
O

(a,b, c, e)
(1)

Grâce à l’expression de I

Ωw
O

, on en déduit l’expression de I

Ω1
B

et I

Ω2
B

et puis celle de I

Ωs
B

:

I

Ωs
B = I

Ω1
B +I

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
, εs)

+I

ΩP
G2

(

he +hms
2

,

ls
2

,

Ls
2

, εs) +m1I(BG1) +m2I(BG2)

où Ls est la largeur de la voile.

2) Matrice d’inertie de (d): On considère que la dérive est composé d’une plaque plane et d’une quille keel. plane est un parallélogramme d’épaisseur εd de masse volumique homogène ρd. keel possède la matrice d’inertie I

keel
G

en son
centre de gravité.

Le plan (O, x,z) (O étant confondu avec le centre de gravité) est un plan de symétrie de plane. Par conséquent, Ixy = Izy = 0 (F = D = 0). Calculons :

xm(z) = −b+zξ , xM(z) = b+zξ ,ξ =

e
2a


FIGURE 12. Paramétrage géométrique d’un paralélipède creux

Iy =

Z

ΩP

(x

2 +z

2
) dm
|{z}
=2dxdzρd

= 2cρd

Z a

z=−a

Z xM(z)

x=xm(z)

(x

2 +z

2
)dxdz

= 2cρd

Z a

z=−a

[

x

3
3

+xz²
]

b+zξ
−b+zξ

dz

= 2cρd

Z a

z=−a

[

2
3

b

3 +2b(ξ

2 +1)z

2
]dz

= cρd

4
3

[b

3
z+b(ξ

2 +1)z

3
]

a
−a

= cρd

8
3

(ab³ + (ξ

2 +1)ba³
)

= mP

2
3

(b

2 + (ξ

2 +1)a

2
)

Où mP = abcρ est la masse de ΩP. On vérifie qu’avec ξ = 0 (parallépipède) on retrouve le moment d’inertie décrit précédemment. On calcul à présent Ix :

∆x = e/2+b, f = −b+e/2

Iz =

Z

ΩP

(y

2 +z

2
) dm
|{z}
=2ρd dxdz

= 2ρd

Z ∆x

x=−∆x

Z c

y=−c

Z −zM(x)

z=−zm(x)

(y

2 +z

2
)dxdydz

= 2ρd

Z ∆x

x=−∆x

Z −zM(x)

z=−zm(x)

2
3

(c

3 +3cz²
)dxdz

On suppose f > 0 : zm(x) = −a pour x ∈ [−∆x,−f ] et zm(x) = −a+ (x+ f)ξ pour x ∈ [−f,∆x]. Par ailleurs, zM(x) = a + ξ (x − f) pour x ∈ [−∆x, f ] et zM(x) = a pour x ∈ [ f,∆x]. Calculons J
Iz
2cρd

=

Z −f

x=−∆x

Z a+ξ (x−f)

−a

2
3

(c

3 +3cz²
)dxdz

+

Z f

x=−f

Z a+ξ (x−f)

−a+ξ (x+f)

2
3

(c

3 +3cz²
)dxdz

+

Z ∆x

x=f

Z a

−a+ξ (x+f)

2
3

(c

3 +3cz²
)dxdz

=

2
3

Z −2ξ f

u=−ξ (∆x+f)

(A0 +A1u+A2u

2 +A3u

3
)
| | {z | }
| u=ξ (x−f)

du

+

2
3

Z f

x=−f

(B0 +B1x

2
)dx

+

2
3

Z ξ (∆x+f)

u=2ξ f

(A0 −A1u+A2u

2 −A3u

3
)
| | {z | }
| u=ξ (x+f)

du

=

4
3

[A0(uf −ui) + A1
2

(u

2
f −u

2
i

)] + A2
3

(u

3
f −u

3
i

) + A3
4

(u

4
f −u

4
i

)]

+

4
3

[B0 f +

B1
3

f

3
]

uf = ξ (∆x + f)
ui = 2ξ f
A0 = 2(ac³ +ca³
)

A1 = c

3 +3ca²

A2 = 3ac

A3 = c

B0 = ac(2c

2 +2a

2 −3aξ f +6ξ

2
f

2
)−2c

3
f ξ −2ξ

3

c f ³

B1 = 6c(aξ

2 −ξ

3
f)

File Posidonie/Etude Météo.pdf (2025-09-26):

# ETUDE DE LA TENUE EN MER DE Posidonie

Théo Prats Rioufol, Mai 2025.

Résumé—Ce documment présente l’analyse menée sur les conditions météo que Posidonie devrait confronter. A défault de pouvoir adapter la géométrie de la coque à toute les condition de mer, ce document vise à déterminer le cade de navigation de Posidonie, et de localiser les effort causé par les vagues. Ainsi, l’opérateur connaitera quelle seront les conditions de mer limites, et le concepteur aura les paramètres critiques en tête.
Index Terms—Sea keeping, wave theory, wave diffraction analysis, hydrodynamic response
I. INTRODUCTION

Pour cette étude, on cherche à répondre à trois objectifs : — Trouver le domaine de navigation, c’est-à-dire les conditions de mer pour lesquels le bateau peut "survivre" (ne pas subir de dommage par la houle), et celle où il peut naviguer
— Quantifier les efforts due aux vagues
— Obtenir une loi quantitative pour améliorier les performance du bateau.
La réponse du bateau sera déterminée grâce au module AQWA d’Ansys. Les données d’entré du modèle sont : la période des vagues T, la hauteur des vagues h, la direction par rapport au bateau α, la vitesse du bateau u (modélisé par un courant). On néglige l’action du vent sur le bateau (on se concentre uniquement sur la réponse au vagues).

II. TAILLE ET PÉRIODE DES VAGUES

A. Cadre d’étude

Pour trouver la taille et la période des vagues à considérés, on s’appuie sur des enregistrements de la houle en méditerranée et en atlantique grâce à l’initiative européenne Copernicus. Ainsi, on définit 5 zones d’intérêt (voir Fig. ?? :

1) Le canal région PACA vers la Corse. La zone 1 moyenne les vagues rencontrés lors d’une traversée de 300km jusqu’en Corse
2) A mi-chemin France-Algérie, dans le but de capter le comportement des vagues de haute mer
3) Le large de Perpignan, dans le cas où le bateau serait envoyé dans cette direction
4) Les côtes bretonnes, souvent utilisé comme départ vers la MicroTransat. Par ailleurs les vagues venues d’atlantique vienne se briser sur ces côtes, avec une grande puissance.
5) Au « large » en Atlantique, au-dessus des îles Açores comme exemple des vagues d’océan

On moyenne spatialement 4 grandeurs sur chacune de ces zones :

— Sea surface wind wave mean period (VTM01_WW) correspondant à la période moyenne des vagues générées par le vent local.
— Sea surface wind wave significant height (VHM0_WW) soit la hauteur significative (la moyenne des 1/3 vagues les plus grandes, mesuré du creux jusqu’à la crête) de ces mêmes vagues.
— Sea surface primary swell wave significant height (VHM0_SW1) idem pour la houle (générée par un vent/orage lointain). Elle est très régulière est la période est longue. On notera que sa direction peut être opposée aux vagues générés par le vent local qui peut faire déferler ces vagues. « Primary » corresponds au fait que l’on considère que les vagues dans la direction principale de la houle.
— Sea surface primary swell wave mean period (VTM01_SW1) idem avec la période moyenne.
B. Distribution générale de la taille des vagues


FIGURE 2. Histograme normalisé (l’intégrale des courbes est unitaire) de la taille de la houle dans la direction principales pour différentes zones géographiques.

La figure II-B présente un histogramme de la taille de la houle sur chacune des zones. En méditerranée (zone 1,2 et
3) la houle est inférieure 51cm à m dans 50% des cas, 1.39m dans 90% des cas, 1.83m pour 95% et inférieure à 2.62m pour 99% des cas (sur une durée d’environ 200 jours). En atlantique, c’est 1.7m pour 50%, 3.36m pour 90%, 4.03m sous les 95% et 99% de la houle est inférieure à 5.34m. On remarquera que les côtes bretonnes sont particulièrement houleuses en moyenne (médiane autour de 2.66m contre 40cm pour la région PACA). Pour posidonie en méditerranée, on retiendra h = 2.62m.


FIGURE 3. Histograme normalisé (l’intégrale des courbes est unitaire) des tailles de vague causé par le vent pour différentes zones géographiques.

La figure II-B présente un histogramme de la taille de la mer formée par le vent sur chacune des zones. On remarque que la distribution est d’avantage tassée vers les petites vagues (même si elle sont plus violente, voir la suite). En médiane, en méditerranée, les vagues ont une hauteur de 33cm (20cm pour PACA) versus 83cm pour l’atlantique (1.74m pour la bretagne). En termes d’aspect général, l’histogramme est similaire à celui de la houle. Les hauteurs à 95% et 99% sont de 1.6m, 2.7m en méditerranée et 3.4m, 4.8m en atlantique.

C. Relation taille/période de la houle et du clapot pour chacune des zones


FIGURE 4. Répartition des couples taille/période des vagues (par le vent et principales), pour la zone 1, durant 163 jours.

La figure II-C présente les couples taille, durée des vagues due à la houle (en bleu) et au vent (orange) dans la zone1. On remarque que la déviation sur les vagues formée par le vent est bien plus faible que celle de la houle du fait que la houle peut présenter plusieurs états de « dégénérescence » suivant la distance entre la source de la houle et la mesure (les vagues s’étalent ? la période augmente avec la distance). Si une vague est d’autant plus dévastatrice que sont rapport hauteur/période est grand (forte variation d’amplitude en un temps cours, c-a-d forte accélération/risque de déferler, partie gauche du graphique), c’est la mer formée par le vent qui est dangereuse. Comme pour ces vague la période est bien définie selon la hauteur de la vague, c’est l’histogramme de la mer formé par le vent qui est dimensionnant. Sur la figure II-C, le trait noir en pointillé est une modélisation polynomiale de degré 3 des 10% des vagues les plus courte pour une hauteur donnée (=les plus puissantes).


FIGURE 5. Répartition des couples taille/période des vagues (par le vent et principales), pour la zone 2, durant 290 jours.


FIGURE 6. Répartition des couples taille/période des vagues (par le vent et principales), pour la zone 3, durant 290 jours.

Les figures II-C à II-C trace la même grandeur pour les différentes zones. On remarque qu’en méditerranée les distributions sont plutôt homogènes, tandis que pour l’atlantique


FIGURE 7. Répartition des couples taille/période des vagues (par le vent et principales), pour la zone 4, durant 290 jours.


FIGURE 8. Répartition des couples taille/période des vagues (par le vent et principales), pour la zone 5, durant 290 jours.

(Fig II-C et II-C) la distribution se déplace vers la droite, c-a-d des vagues plus grandes en moyenne mais tout aussi dispersées

D. Autre relations
La figure II-D représente les couples taille-hauteur de la mer formée par le vent, toute zones confondues. On remarque toutes suivent une distribution similaire (c’est un phénomène local, il ne dépend pas de la différence d’étendue océan/mer) que l’on modélise par un polynôme d’ordre 2 :

h = 0.08105T

2 +0.033T −0.052 | (1)

En utilisant le modèle de vague d’Airy pour des houles de faible cambrure pour des profondeurs grandes par rapport à l’amplitude des vagues, la relation de dispersion suivante est satisfaite :

2π
T

2
= gktanh(khw) | (2)


FIGURE 9. Répartition des couples taille/période des vagues formées par le vent, pour toutes les zones. En noir est tracé la modélisation polynomiale d’ordre 3 de la relation taille de la vague - période

TABLE I
MODÈLE DES VAGUES GÉNÉRÉES PAR LE VENT POUR DIFFÉRENTES PÉRIODES.
T [s] | h [m] | L [m] | ||a|| [m/s 2 ] | Pmed (≥) | Patl(≥)
0.50 1.00 1.50 2.00 2.50 3.00 5.00 7.00 8.00 9.00 | -0.02 0.06 0.18 0.34 0.54 0.78 2.14 4.15 5.40 6.81 | 0.39 1.56 3.51 6.25 9.76 14.05 39.03 76.50 99.92 126.47 | 0.19 0.39 0.75 1.06 1.35 1.63 2.69 3.73 4.24 4.75 | 100.00% 85.31% 66.22% 49.59% 34.96% 24.24% 2.73% 0.09% 0.00% 0.00% | 100.00% 92.59% 84.76% 74.66% 63.05% 52.21% 18.87% 2.87% 0.26% 0.03%

où hw est la profondeur de l’eau ; k = 2π/L le nombre d’onde ; g l’intensitée de pesanteur ; L la longeur d’onde (donc celle de la vague) et T la période de la vague. On se considère suffisament loin des côtes tel que khw → +∞ d’où :

L =

g
2π

T

2
(3)

On notera que le modèle d’Airy peut mener à des inprécision en eau profonde de l’ordre de 30%. En assimilant la vague à une signusoide (hypothèse sous dimentionnante), on peut caluler l’accélération d’une bouée fixe qui suivrait le mouvement de la vague : ||a|| = 2πh/T. La table II-D présente le caluls des grandeur caractéristique d’une vague pour plusieurs période. Pmed(≥) (resp. Patl(≥)) désigne la probabilité qu’une vague causée par le vent en méditéranée (resp. en atlantique) tirée au hazard soit d’amplitude plus grande que h.

III. TENUE EN MER DE POSIDONIE

A. Paramétrage de l’étude
L’analyse de la tenue en mer de Posidonie s’effectue sur Ansys avec le module Diffraction hydrodynamique et Réponse hydrodynamique d’AQWA. La figure III détaille le paramétrage

CdGboat; Iboat; mcomp; mhull; CdGhull

FIGURE 10. Paramétrisation géométrique du bateau sous Ansys AQWA.

TABLE II
DIMENTIONEMENT GÉOMÉTRIQUE DE POSIDONIE
Composant | Dimmentionement
Voile Dérive Lest CdG Iboat ze | 0.3m × 1.17m, ds = 0.2m, 45% Trapèze, 0.15m × 1m × 0.01m, 30°, 30% 40kg zCdG,boat\hull = −0.98 63.51 0 −6.72 2 0 64.56 0 kg/m −6.72 0 11.05 30 mm

géométrique. L’origne du repère est situé à une distance ze du centre de gravité de la coque, avec l’axe x vers le sens de la marche et l’axe z opposé au champ de gravité. ze est le niveau du plan d’eau quand le bateau est en équilibre de flotaison. On considère également un angle de tanguage ψ. On considère des vagues se propageant en −x, et pas de courant marin. En effet, on ne cherche à quantifier que la contribution des vague et non la taînée du bateau. On contrain le bateau à ne pas se déplacer selon x et à garder un cap constant. Les masses et inertie utilisées sont détaillées dans la table III-A. Dans AQWA, deux masse ponctuelles en CdGboat et CdGhull ont été placées (avec Ihull ≈ 0 puisque intégrée dans Iboat).

B. Mouvement angulaire face aux vagues
Tout d’abord on s’intéresse à la réponse cinématique du bateau face au vagues. La figure III-B décrit comment le roulis et le tangage sont affecté suivant la période d’une vague. On consière une vague à 60◦ degrés d’incidence (0◦ correspondant à une vague arrivant sur la proue du bateau). Le courbe en trait plein représente de combient le bateau va s’incliner par unité de taille de vague incidente. Les courbes en pointillées représentent la réponse pour une vague typique méditéranéenne ayant une taille h = f(T) (d’après l’eq. (1)). Ainsi pour les petites périodes (vagues courte) la réponse "réelle" est moins critique que celle théorique (trait plein) car les vagues de ces périodes sont d’amplitude faible. A contrario, l’amplitude des vagues augmente à la période d’où les perturbation angulaire plus importantes pour T ≥ 2s jusqu’à stationner à 7m avec la pente d’une décade. Les zones semi

Wave period; Roll @60◦; Pitch @60◦; Rotation

Rotation Per Unit of Wave Amplitude

FIGURE 11. Réponse en roulis et tanguage du bateau face à une vague en fonction de la fréquence. Les zones semi transparentes bleu et noir décrivent l’instabilité en tanguage et roulis respectivement

Divergence Stable

FIGURE 12. Réponse angulaire du bateau face au solicitation des vagues. Les angles de la polaire correspondent à l’angle d’incidence des vagues, le rayon à leur fréquence et la couleur à l’amplitude de la réponse. La taille des vagues est déduite de la période d’après le modèle de la partie précédente.

transparente correspondent au zone d’instabilité du bateau (celle du roulis est atteinte pour des angles important car un bateau gîte plus que ce qu’il tangue). Les deux traits magenta décrivent les zone statistiquement atteinte par les vagues en méditéranée : dans 50% des cas, les vagues ont une période supérieure à 5s (trait de droite) et dans 97% des cas, ≥ 2s (à gauche). Ainsi l’instabilité en tanguage n’est pas un problème (car à droite de la ligne des 97%) c’est le roulis qui est limitant. La figure III-B est essentiellement une représentation angulaire de la figure III-B. Les angles du graphe représentent l’angle d’incidence de la vague (0◦

: vagues de face, 90◦
tribord...), la distance au centre est la fréquence de la vague incidente (l’extérieur du graphe représente les vagues de courte période) et la couleur est l’amplitude du mouvement du bateau

Force [N]

FIGURE 13. Effort dans le sens longitudinal en fonction de l’angle d’incidence des vagues et de leur période. La taille des vagues est calculé avec le modèle de vague méditéranéen.

(cumulant roulis et tanguage). On constate que le graphe est symétrique en y (car la coque est symétrique) et présente quatre lobes : ceux du roulis (lobes au centre, exité par les vagues latérales) et ceux du tranguage (à l’extérieur, solicité pour une fréquence plus grande, en cohérence avec la fig. III-B). La hauteur des vague est également calculé à l’aide de l’eq. (1) saturée à 7m. Les deux cercles au centre délimitent les périodes contenant 50% et 97% des vagues méditéranéennes. (il faut regarder le disque décrit par ces cerles, d’une fréquence de 0Hz (vague très étallée) à 0.5,0.2Hz). Ce qui se trouve en dehors du plus grand cercle (lobe de tanguage) n’est solicité que dans moins de 3% des vagues. Toutefois, la dérive (non modélisé) joue un rôle majeur dans l’amortissement du roulis.

C. Forces exercée par les vagues
Dans un second temps, on quantifie l’effort transmit par la vague sur le bateau. La figure III-C présente une polaire des isosurface de force transmit sur l’axe longitudinal du bateau, en fonction de la fréquence et l’angle d’incidence de la vague. La taille des vagues est donnée par le modèle méditéranéen saturé à hmax = 7m. On remarque la présente de deux lobe pour les vagues venant sur la proue et la poupe. Le lobe de la poupe (180◦
) est plus large que celui de la proue. En effet, sur la coque considéré, l’arrière est bien plus large que l’avant (voir fig. III) ce qui le rend plus sensible au vagues. On note que pour des vagues orthogonale au bateau, presqu’aucun effort n’est transmit dans la direction longitudinale (90◦

et −90◦
).
Les deux cercles réprésentent les mêmes vagues typique des 50% et 97%, le bateau n’ayant pas de problème dans 50% des cas. La figure III-C suit la même logique avec les efforts latéraux. Cette fois ci le graphique est symétrique en x et y, on s’attend aux mêmes efforts au portant (généralement à 135◦

Force [N]

FIGURE 14. Effort dans le sens latéral en fonction de l’angle d’incidence des vagues et de leur période. La taille des vagues est calculé avec le modèle de vague méditéranéen.

des vagues) et au près (45◦
). Les efforts sont maximaux pour une incidence orthogonale (la section vue par les vagues de côté est plus grande que celle de face, et solicite directement le roulis). On constate également que les efforts latéraux sont plus important que ceux longitudinaux : le bateau dérive fortement avec les vagues.
D. Répartition des efforts
La figure III-D présente la répartition des efforts due au vagues, pour une amplitude arbitraire de 0.2m à incidence longitudinale (i = 0

◦

) et latérale (i = 90◦
). Trois fréquences
sont présentées : la fréquence critique en roulis froll = 0.353 Hz, celle en tanguage fpitch = 0.648 Hz et une troisième arbitraire, pour des vagues courtes à f ≈ 1 Hz. On constate que le maximum de la pression est atteind pour les fréquences critiques. De ces graphiques, on déduit que la proue, la poupe et les parties latérales arrière du bateau doivent être renforcées vis-à-vis du centre de la coque, non solicité dans ces 6 configurations.
E. Effet du volume de la carène
Pour qualifier si un coque à grand déplacement (comportant plus de traîné à petite vitesse) est plus performant qu’une à petit déplacement, on simule la réponse au vague pour une coque mise à l’échelle à 83%. Le plan du niveau de l’eau est ajusté pour garder un même volume en eau (compensant 10kg de coque et 38.7kg de composants). Ainsi, on obtient une nouvelle carène avec la même capacitée d’emport que la précédente, mais un volume hors de l’eau plus faible. (Ainsi qu’un couple de redressement plus modeste).
La figure III-E représentente la sensibilité angulaire en fonction de l’angle d’incidence des vagues et de leurs fré-

f = froll = 0.353 Hz | f = fpitch = 0.648 Hz | f = 0.986 Hz

pmax = 0.3×10³ N/m²; pmax = 15.4×10³ N/m²; pmax = 3.1×10³ N/m²

pmax = 5.3×10³ N/m²

pmax = 1.0×10³ N/m²
pmax = 1.8×10³ N/m²

FIGURE 15. Répartition des efforts sur la coque en fonction de la fréquence, pour des vagues longitudinales (i = 0

◦

) et transversales (i = 90◦
). Les pressions
sont à titre indicatif, et ont été obtenue avec une amplitude de 0.2m

Divergence Stable

FIGURE 16. Réponse angulaire de la coque à fort déplacement face au solicitation des vagues. On constate que la zone d’instabilité du roulis à diminué angulairement et s’est étalée fréquenciellement.

quences (analogue de la figure III-B). On constate que le bateau comporte toujours une instabilité en roulis mais celle ci atteind des valeurs maximale plus faible que pour la coque à faible déplacement. La zone d’instabilité s’est légèrement élargie en fréquence mais à diminuée en angle d’incidence des vagues (120◦ vs 170◦
). Rappelons que le bateau navigue la plupart du temps entre 45◦

et 135◦ des vagues.

Les figures III-E et III-E représentent respectivement les différences de performance entre la carène à faible (CFaible) et fort (CFort) déplacement pour l’axe longitudinal et latéral respectivement. Ces figures tracent les efforts CFaible−CFort. Ainsi une valeur positive signifie que la carène à faible déplacement performe mieux que CFort. On constate que pour l’axe longitudinal, CFaible réduit les efforts pour toutes les vagues avec une probabilité d’occurence supérieure à 3%. L’opposé se produit pour l’axe latéral (voir fig. III-E) avec une augmentation modérée des efforts sur tout le domaine. (la

Force [N]; 40Worse than original Better

FIGURE 17. Différence d’effort longitudinal entre la carène à fort déplacement et celle à petit déplacement en fonction de l’angle d’incidence des vagues et de leur période. Une valeur positive signifie que la carène à fort déplacement subie moins d’effort.

seule réduction se produit pour les vagues arrivant de l’arrière à hautes fréquence).

F. Effet de l’angle des parois de carène et de l’inertie
On considère à présent une coque en forme de trapèze extrudé (voir fig. III-F). On cherche à quantifier la réponse de la carène aux vagues latérales wi (incidence normale sur le bateau) selon différents angle d’inclinaison θ des parois latérales du bateau. Les parois sont inclinés en gardant la largeur l du bateau à mi tirant d’eau constante, de telle manière à garder le volume déplacé V0 constant. V0 = 126L à h = 0.2m, l = 0.68m, L = 1.87m. Le centre de gravité est placé à une altitude h = −0.8m en dessous du centre géométrique de (h) avec une masse équilibrant verticalement le bateau est une inertie Ixx = Iyy = 50Nm²

, Izz = 10Nm²
(produit d’inertie nuls).
La figure III-F traces les efforts F par unité d’amplitude de la vague wi selons l’axe y en fonction de la fréquence f de

Force [N]; 40Worse than original Better

FIGURE 18. Différence d’effort latéral entre la carène à fort déplacement et celle à petit déplacement en fonction de l’angle d’incidence des vagues et de leur période. Une valeur positive signifie que la carène à fort déplacement subie moins d’effort.

θ

l

L

V0 water

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
FIGURE 19. Géométrie de la carène considérée pour l’étude de l’inclinaison des parois et de l’inertie. La coque est un parallélograme extrudé, dont les parois sont incliné d’un angle θ à l constant. Ainsi, le volume déplacé V0 est constant avec θ.

angles; forces; Force [N/◦]; wi frequency; Angular mouvement [◦/◦]

FIGURE 20. Effet de l’angle des parois de la coque sur la sensibilité angulaire et les forces exercé par une vague latérale wi

roll; flongitudinal; pitch; flateral; Mean Force [N]; Angular Amplitude [◦]; Ixx, Iyy Inertia [N/m

FIGURE 21. Effet de l’inertie sur le tangage, le roulis et les forces longitudinale et latéral de résistance des vagues.

wi sur l’axe de droite. L’axe de gauche représente le roulis Φ par unité d’amplitude de la vague wi en fonction de f . On constate que la sensibilité angulaire est faiblement dépendante de θ tandis que les efforts augmentent avec θ → 90◦
. Une
coque à parois à faible incidence est à privilégier.
La figure III-F décrit l’effet de l’inertie Ixx = Iyy = I sur les forces et mouvements angulaire de la coque. Pour cela, on considère une vague test wt à 45◦ d’incidence, d’amplitude 0.17m, de période 2s et une force de 20N qui tracte le bateau dans sa direction longitudinale. L’amplitude de 45◦ souhaite
représenter un bateau navigant au près. On constate que le bateau gîte de plus en plus fort à mesure que l’inertie augmente (courbe verte). Le tanguage reste inchangé (courbe noire). Par ailleurs le bateau tends à moins être freiné avec une faible inertie, puisque la force longitudinale (en bleue) aumente avec l’inertie. Toutefois, une grande inertie permet de moins dériver, puisque la force latérale décroit avec l’inertie (bateau moins déporté dans le sens des vagues). En gardant en tête qu’un bateau rapide dérive moins (plus de force antidérive à incidence fixe) et qu’une petite inertie réduit la résistance des vagues dans le sens de la marche, on priviligéra une faible inertie.

IV. CONCLUSION

Dans ce document, l’analyse statistique des vagues en méditéranée et en atlantique en section II à montré que les vagues les plus critique vis-à-vis de Posidonie ; i.e de forte fréquence et amplitude ; étaient celle généré par le vent. La houle, est systèmatiquement de période plus grande à hauteur de vague donné. La taille de la mer généré par le vent peut être lié à sa période grâce à une relation polynomiale, permettant de caractériser la réponse d’une coque uniquement selon la période et la direction des vagues incidentes.
L’étude de Posidonie sur Ansys AQWA à révélé que le bateau présente une instabilité en roulis (f = 0.353 Hz) et non en tanguage, pour 97% des vagues. Les efforts générés par les vagues sont maximum pour l’axe du roulis et asymétrique vis à vis de l’avant et l’érrière de la carène. (significativement moins d’effort pour les vagues de face). Les efforts sont majoritairement localisé à la proue, poupe et latéralement, au niveau de la partie la plus large de la coque.
En réduisant le volume de la partie imergé par rapport à celle émergé, la stabilité en roulis est améliorée, les efforts en tanguage sont réduit et ceux en roulis légèrement augmenté. L’étude de l’angle des parois montre qu’un profil très vouté est préférable à des parois en angle droit. Enfin, il a été montré qu’une faible inertie est à privilégier.

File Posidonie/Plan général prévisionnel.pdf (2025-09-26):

résister 2; : Moteur électrique en cas de pétole; 3 contraintes de la coque 4; naturellement (aileron droit) la voile; à la bonne incidence; : Girouette; : Caméra pour éviter les obstacles; : Feu de position; Architecture Hardware

: Coque optimisée pour la vitesse, un fort couple de redressement, faiblement ralentit par les vagues, solide pour à une collision, un échouage et les vagues
/ situation critique
: Quille qui s’attache au pied de mat pour soulager les . Inclinée pour passer des obstacles : Protège safran inclinée pour ne pas trainer de déchets

/
algues 5 : Safran suffisamment grand pour donner un bon effort de

commande dans les petites vitesses 6 : Case à équipement externe : AIS, Satellite, GPS
. Contient
une batterie de secours pour partager la position du drone 7 : Mat en carbone pour que la flexibilité le rende plus

résilient en cas de choc violent dans les vagues

. La voile
tourne librement selon une amplitude de 180

° (bloqué pour
le portant) mais peut dépasser cette limite en cas de choc (loquet qui se déverrouille pour éviter la casse) 8 : Voile rigide coulissante pour s’adapter au vent 9 : Panneau solaires A : Aileron de commande de l’angle de la voile

: Girouette de coque (redondance) et anémomètre

## Hardware

1 : Panneau solaire de coque 2 : Crochet de remorquage

Système voile; Système communication; Système navigation; • Module communication satellite • Module GPS • Module GSM • Module communication courte portée; • Moteur aileron • Panneau solaire • Girouette • Encodeur magnétique de la position de la voile; Hémisphère Gauche • Batterie plomb • Panneau solaire • IMU, Magnétomètre • GPS • Ordinateur de bord; Direction : • Encodeur Magnétique • Potentiomètre Propulsion : • Moteur électrique Capteur : • Girouette, Anémomètre; • Moteur DC • Moteur brushless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

- Batterie de secours (non rechargeable)
- Moteur de prise de riz | • Protection contre les surcharges de l’alimentation

* Aucun des deux hémisphère utilisent les mêmes références de composants. Ils ne sont pas dans les mêmes compartiments étanches et sont isolées électriquement.

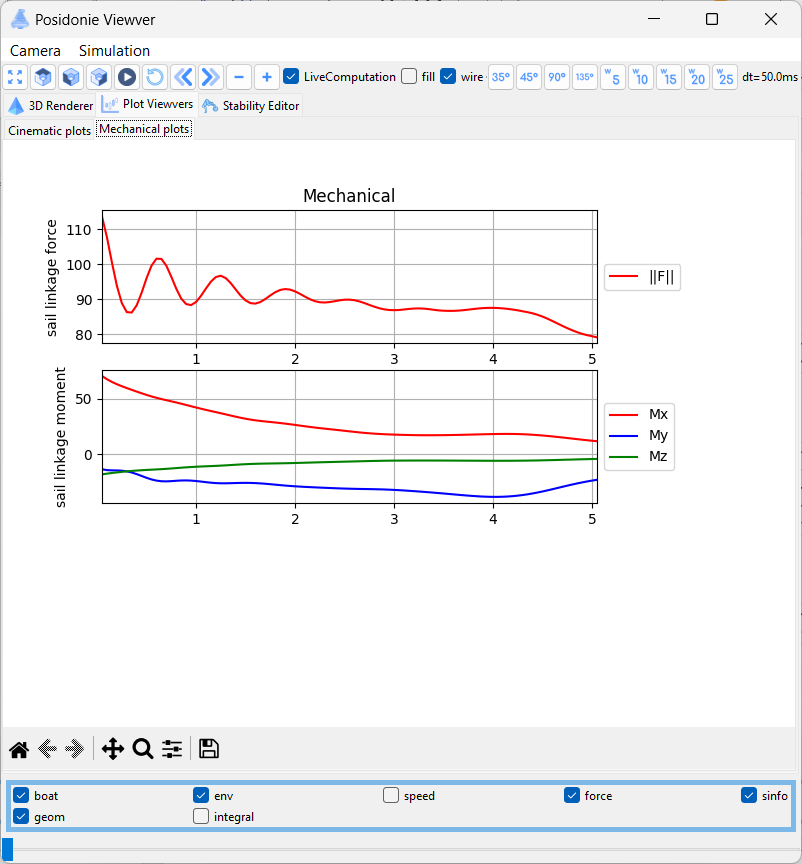
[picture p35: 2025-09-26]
Posidonie/Photos/VPP-MechanicalLoads.png

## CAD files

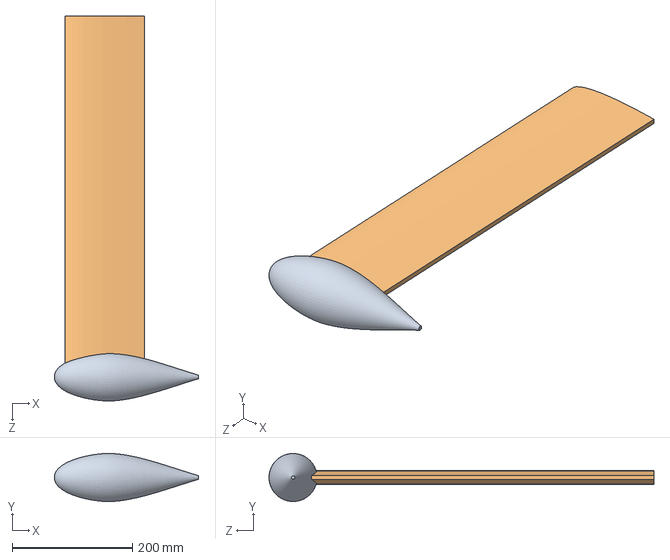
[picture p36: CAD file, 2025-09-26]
Posidonie/CFD - Drift/DeriveEtBulbe.SLDASM
240.0 x 79.9 x 640.0 mm
Airfoil
BulbeDerive

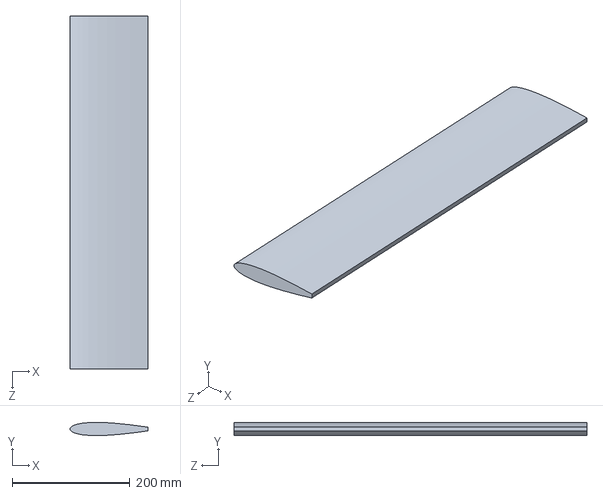
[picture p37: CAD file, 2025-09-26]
Posidonie/CFD - Drift/Airfoil.SLDPRT
132.6 x 22.5 x 600.0 mm

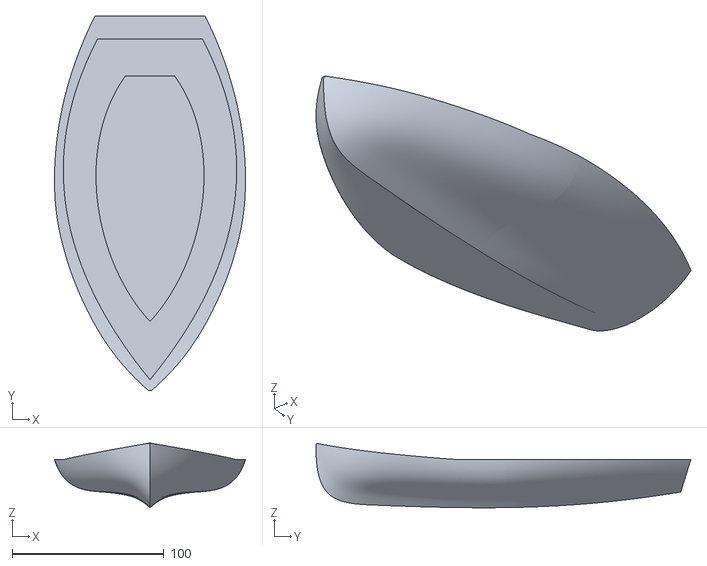
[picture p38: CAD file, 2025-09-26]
Posidonie/VPP Program/backend/hull/RowingBoat.stl
125.8 x 246.8 x 42.5

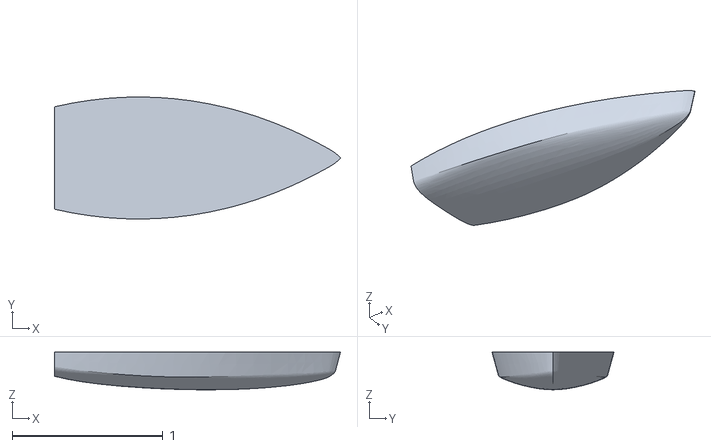
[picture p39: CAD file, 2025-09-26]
Posidonie/VPP Program/export/goodOrientation.stl
1.90 x 0.811 x 0.25

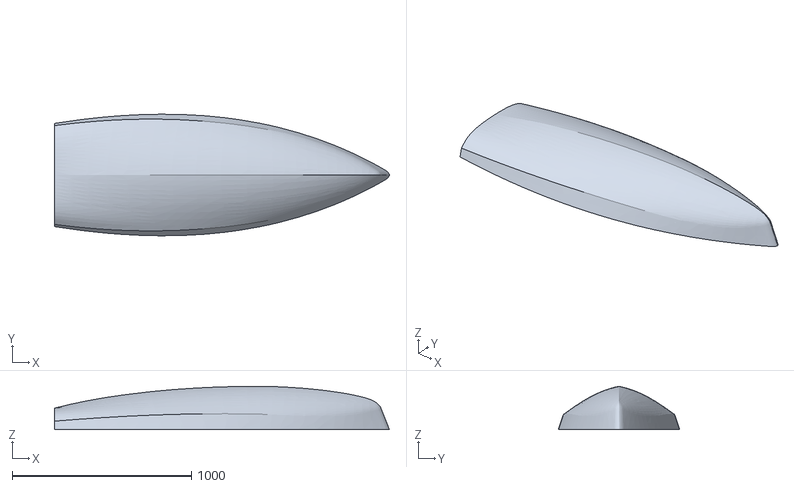
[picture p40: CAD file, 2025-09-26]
Posidonie/VPP Program/HullV5.STL
1871.3 x 679.0 x 242.1

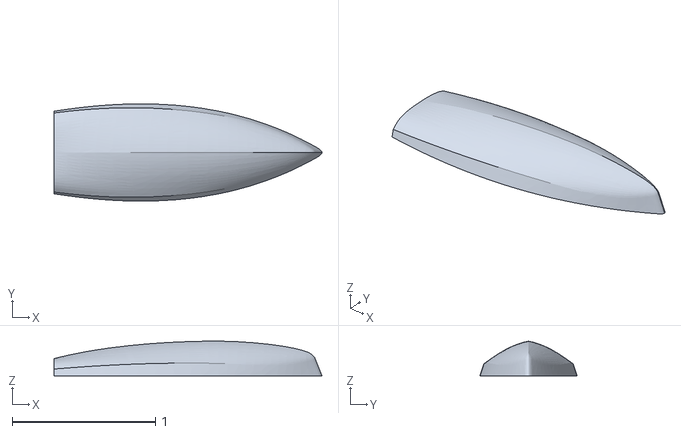
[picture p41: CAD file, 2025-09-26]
Posidonie/VPP Program/backend/hull/moved.stl
1.87 x 0.679 x 0.242

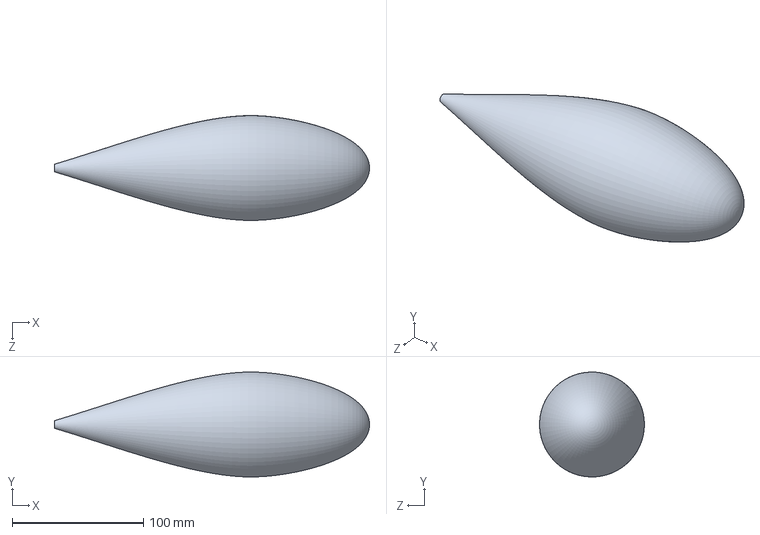
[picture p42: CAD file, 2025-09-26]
Posidonie/CFD - Drift/BulbeDerive.SLDPRT
240.0 x 79.9 x 79.9 mm

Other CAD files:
Posidonie/CFD - Hull/Drag Analysis/hull_drag_sym_fast_1dof_rot_files/dp0/FFF/Fluent/libudf/win64/3d_host/HullUDFV2.obj
Posidonie/CFD - Hull/Drag Analysis/hull_drag_sym_fast_1dof_rot_files/dp0/FFF/Fluent/libudf/win64/3d_node/HullUDFV2.obj
Posidonie/CFD - Hull/Drag Analysis/hull_drag_sym_fast_1dof_rot_files/dp0/FFF/Fluent/libudf/win64/3d_host/udf_names.obj
Posidonie/CFD - Hull/Drag Analysis/hull_drag_sym_fast_1dof_rot_files/dp0/FFF/Fluent/libudf/win64/3d_node/udf_names.obj
Posidonie/CFD - Hull/Drag Analysis/hull_drag_sym_fast_1dof_rot_files/dp0/FFF/Fluent/libudf/win64/3d_host/HullUDF.obj
Posidonie/CFD - Hull/Drag Analysis/hull_drag_sym_fast_1dof_rot_files/dp0/FFF/Fluent/libudf/win64/3d_node/HullUDF.obj
Posidonie/CFD - Drift/DeriveEtBulbe.IGS

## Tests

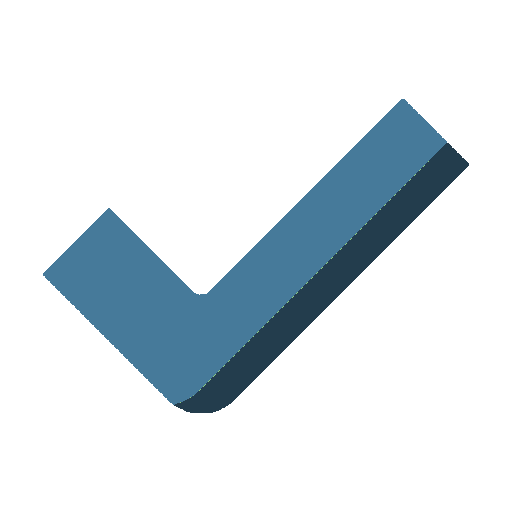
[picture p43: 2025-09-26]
Posidonie/VPP Program/utils/res/validate.png

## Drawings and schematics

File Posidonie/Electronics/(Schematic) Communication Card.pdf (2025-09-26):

# B8 12 B7 13 B6 14 B5 15 B4 16 B3 17 B2

## ADJ/GND

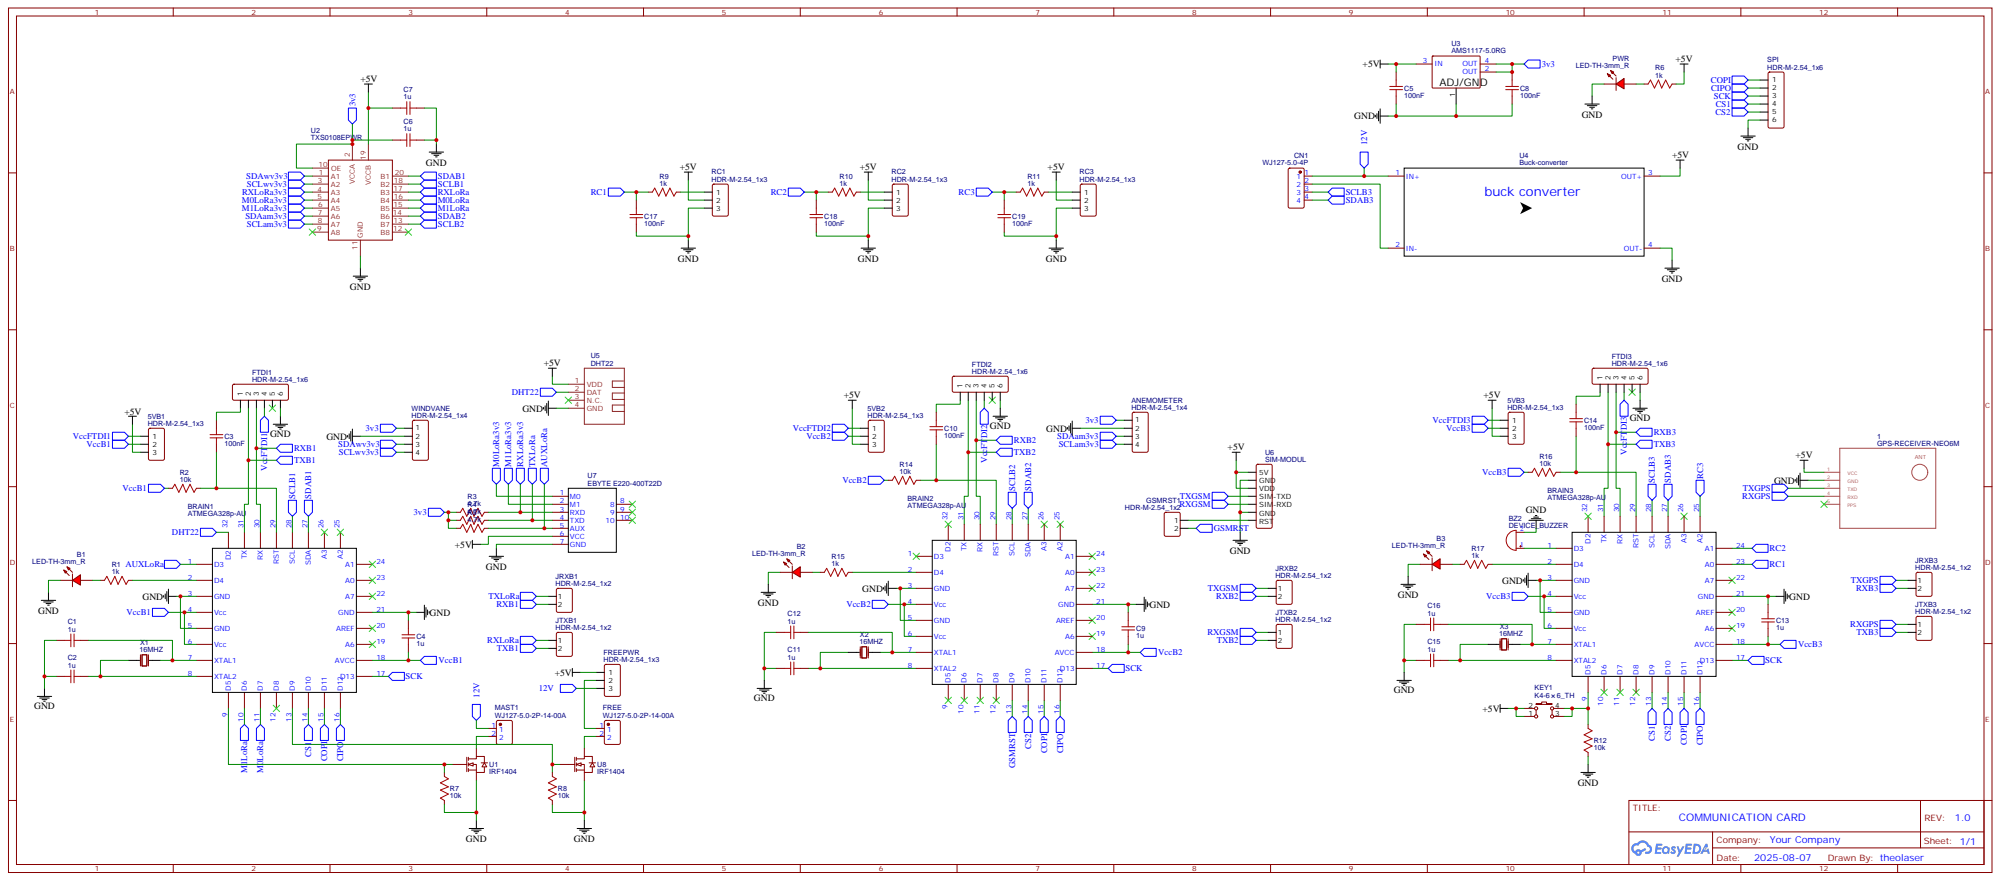
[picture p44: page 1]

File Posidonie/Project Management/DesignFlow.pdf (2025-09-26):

## Structural simulation Shape

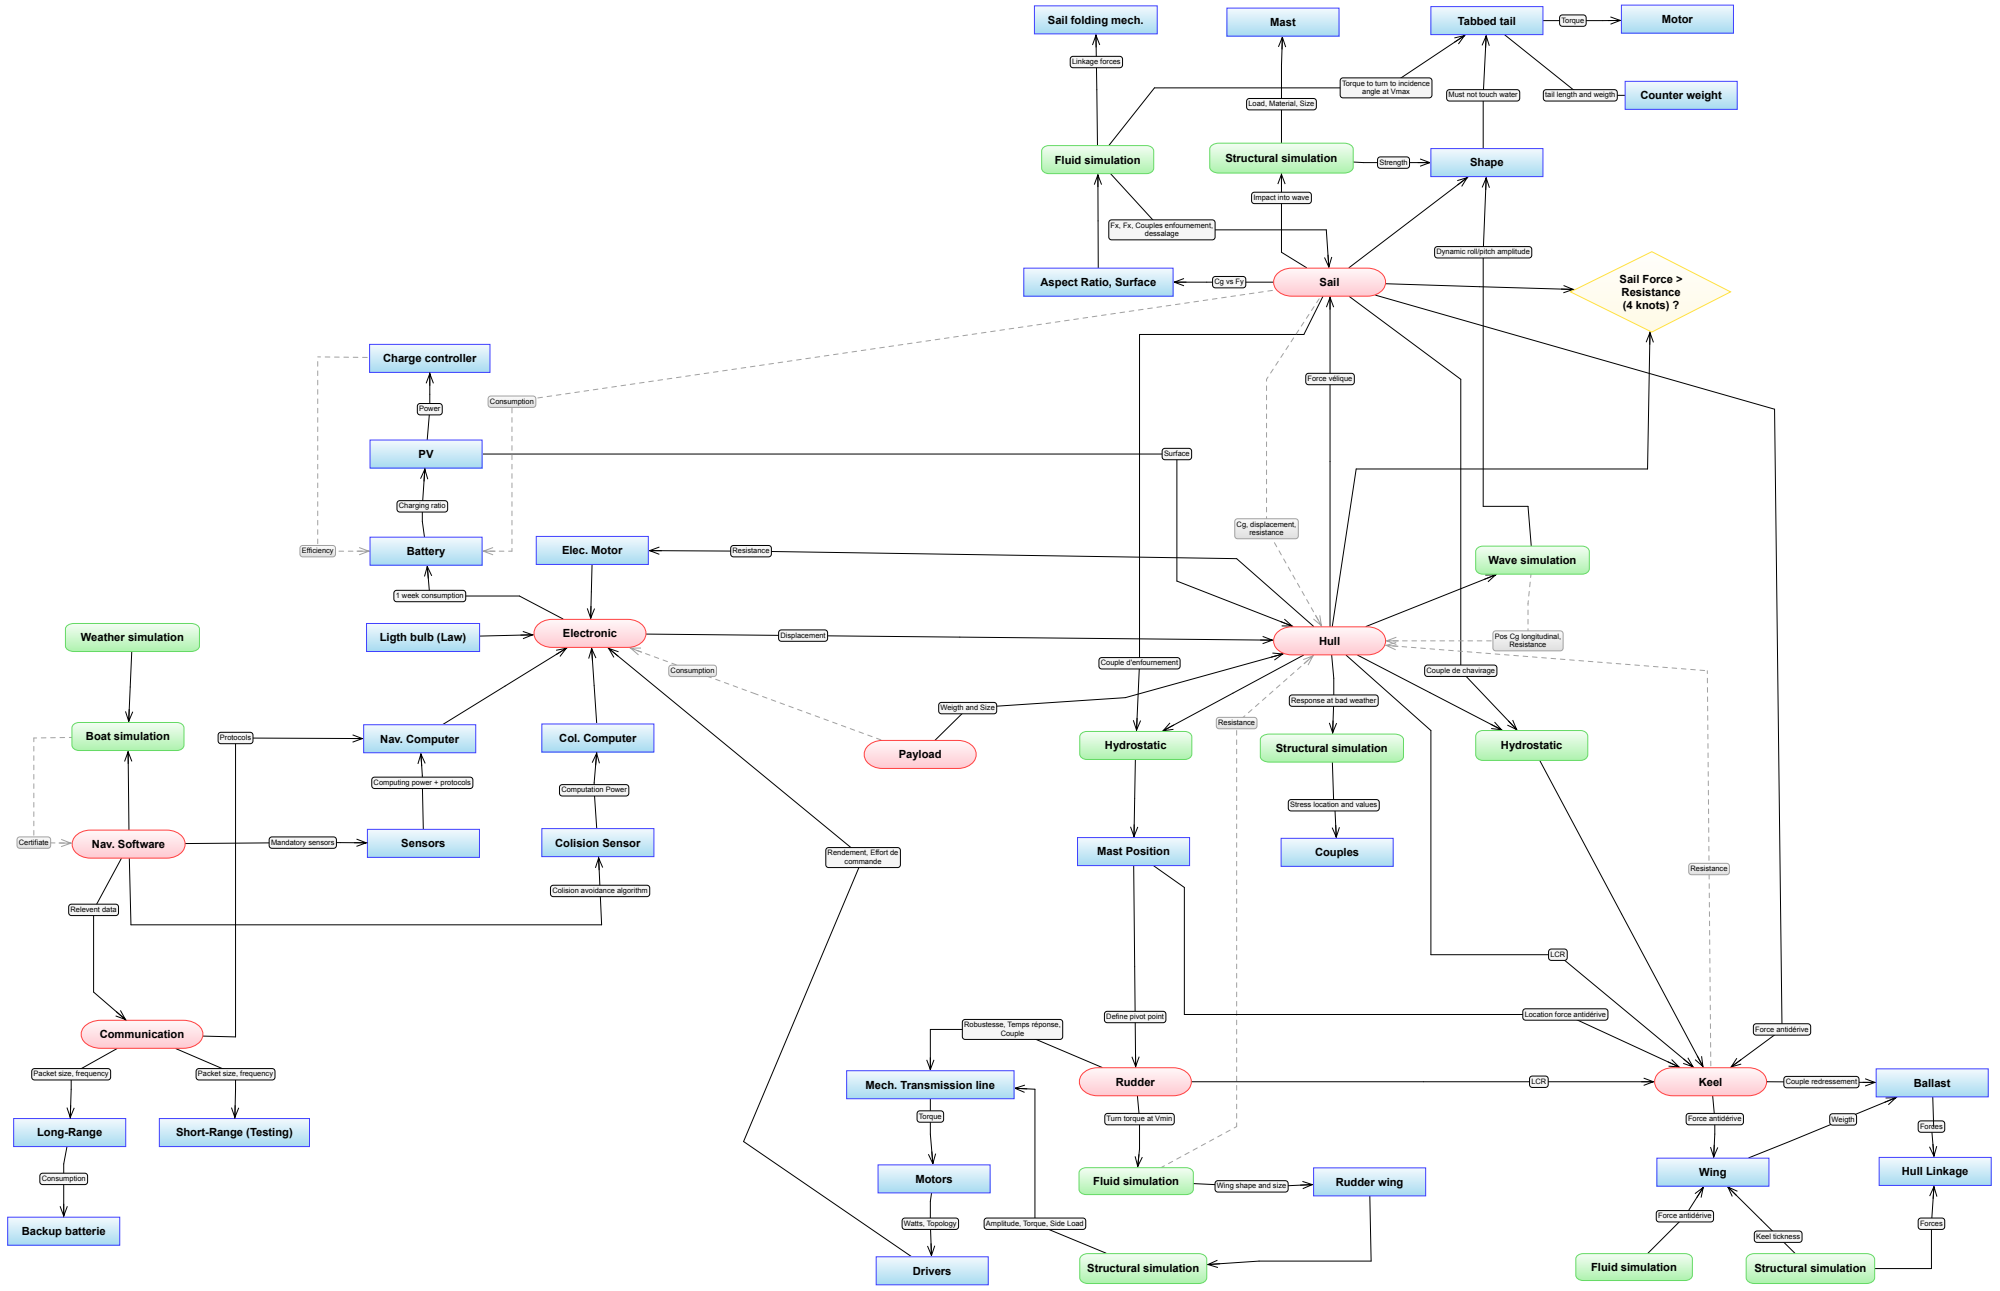
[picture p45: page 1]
Col. Computer; Computation Power; Colision Sensor; Protocols; Backup batterie; Consumption; Long-Range; Communication; Relevent data; Certifiate; Nav. Software; Mandatory sensors; Sensors; Displacement; 1 week consumption; Couple de chavirage; Hydrostatic; Forces; Hull Linkage; Payload; Weigth; Couple d'enfournement; Elec. Motor; Resistance; Structural simulation; Force antidérive; Keel tickness; Fluid simulation; Strength; Torque; Motor; Efficiency; Charge controller; Power; Surface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

Sail folding mech.

Torque to turn to incidence
angle at Vmax

Load, Material, Size

Impact into wave

Fx, Fx, Couples enfournement,

Dynamic roll/pitch amplitude

Aspect Ratio, Surface

Ligth bulb (Law)

Pos Cg longitudinal,
Resistance

Response at bad weather

Weigth and Size

Computing power + protocols

Stress location and values

Rendement, Effort de
commande

Colision avoidance algorithm

Define pivot point

Location force antidérive

Robustesse, Temps réponse,

Packet size, frequency

Mech. Transmission line

Turn torque at Vmin

Short-Range (Testing)

Wing shape and size

Amplitude, Torque, Side Load

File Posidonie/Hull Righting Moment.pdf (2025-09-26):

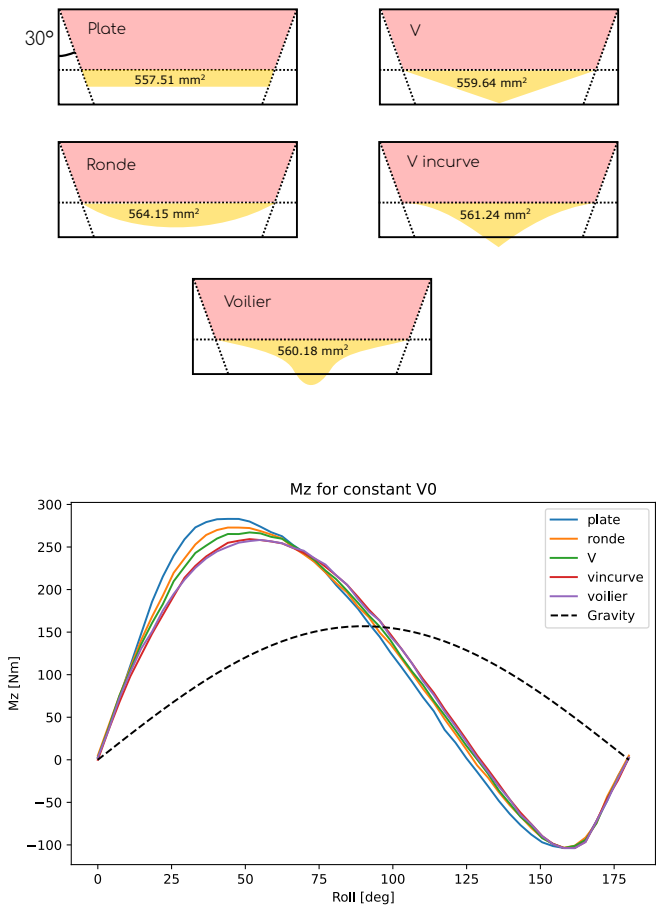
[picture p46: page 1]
557.51 mm²; Plate; 564.15 mm²; Ronde; 559.64 mm²; 561.24 mm²; V incurve; 560.18 mm²; Voilier

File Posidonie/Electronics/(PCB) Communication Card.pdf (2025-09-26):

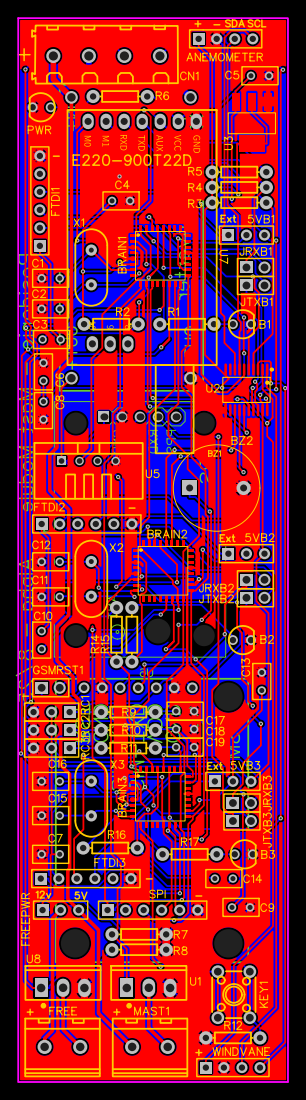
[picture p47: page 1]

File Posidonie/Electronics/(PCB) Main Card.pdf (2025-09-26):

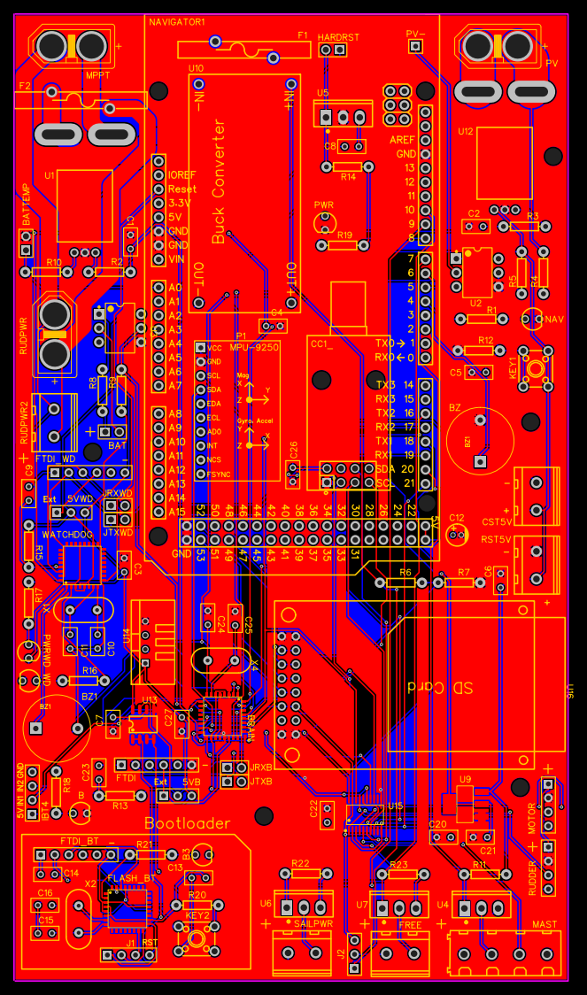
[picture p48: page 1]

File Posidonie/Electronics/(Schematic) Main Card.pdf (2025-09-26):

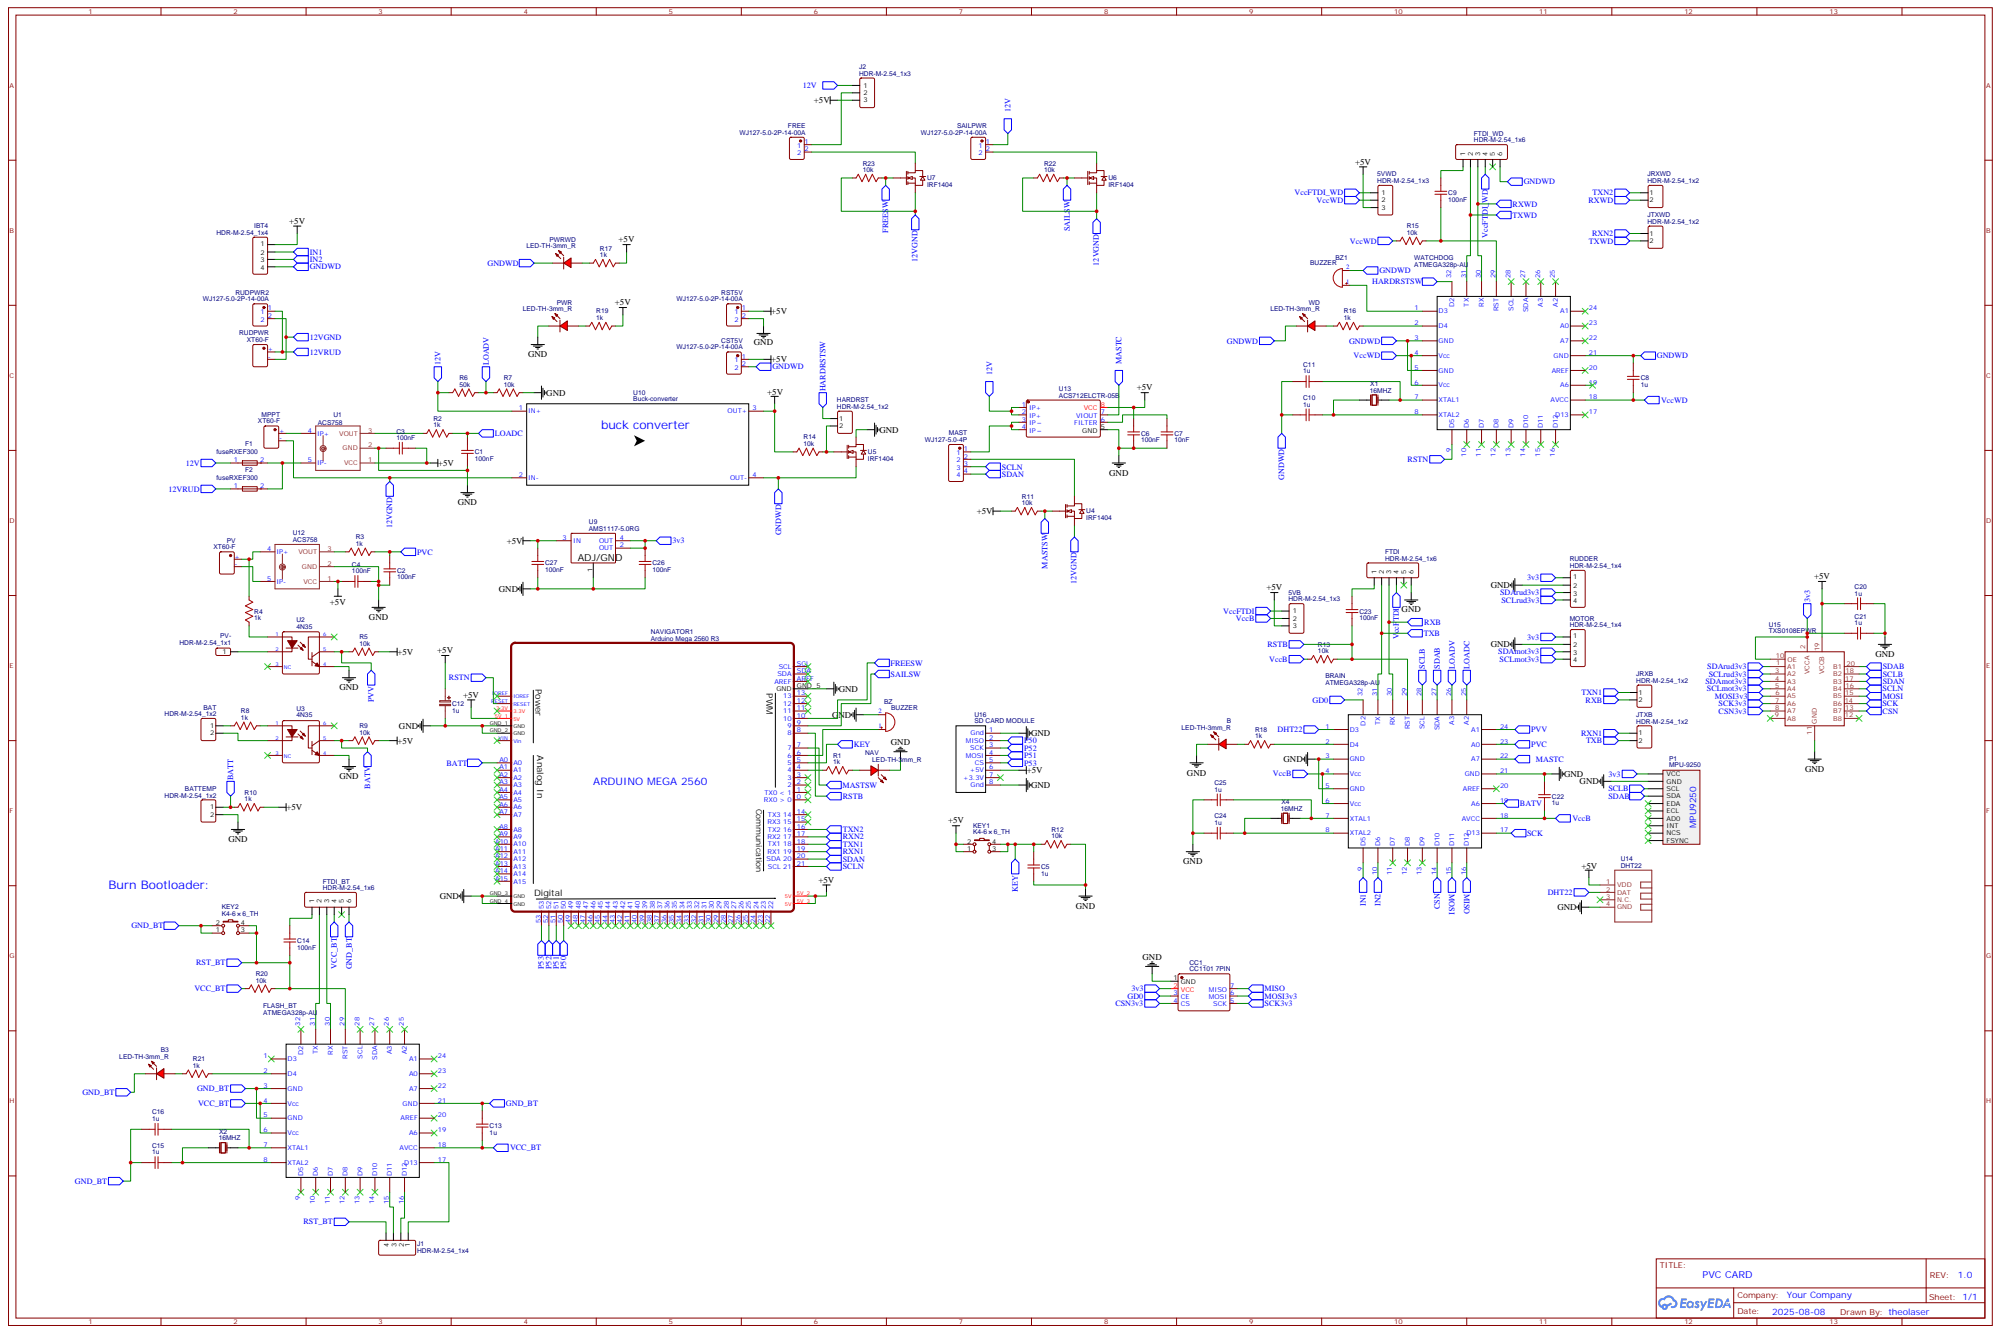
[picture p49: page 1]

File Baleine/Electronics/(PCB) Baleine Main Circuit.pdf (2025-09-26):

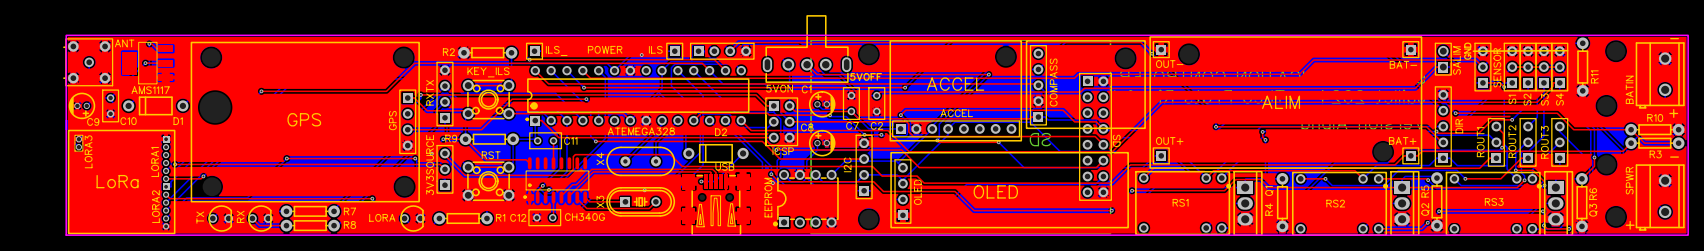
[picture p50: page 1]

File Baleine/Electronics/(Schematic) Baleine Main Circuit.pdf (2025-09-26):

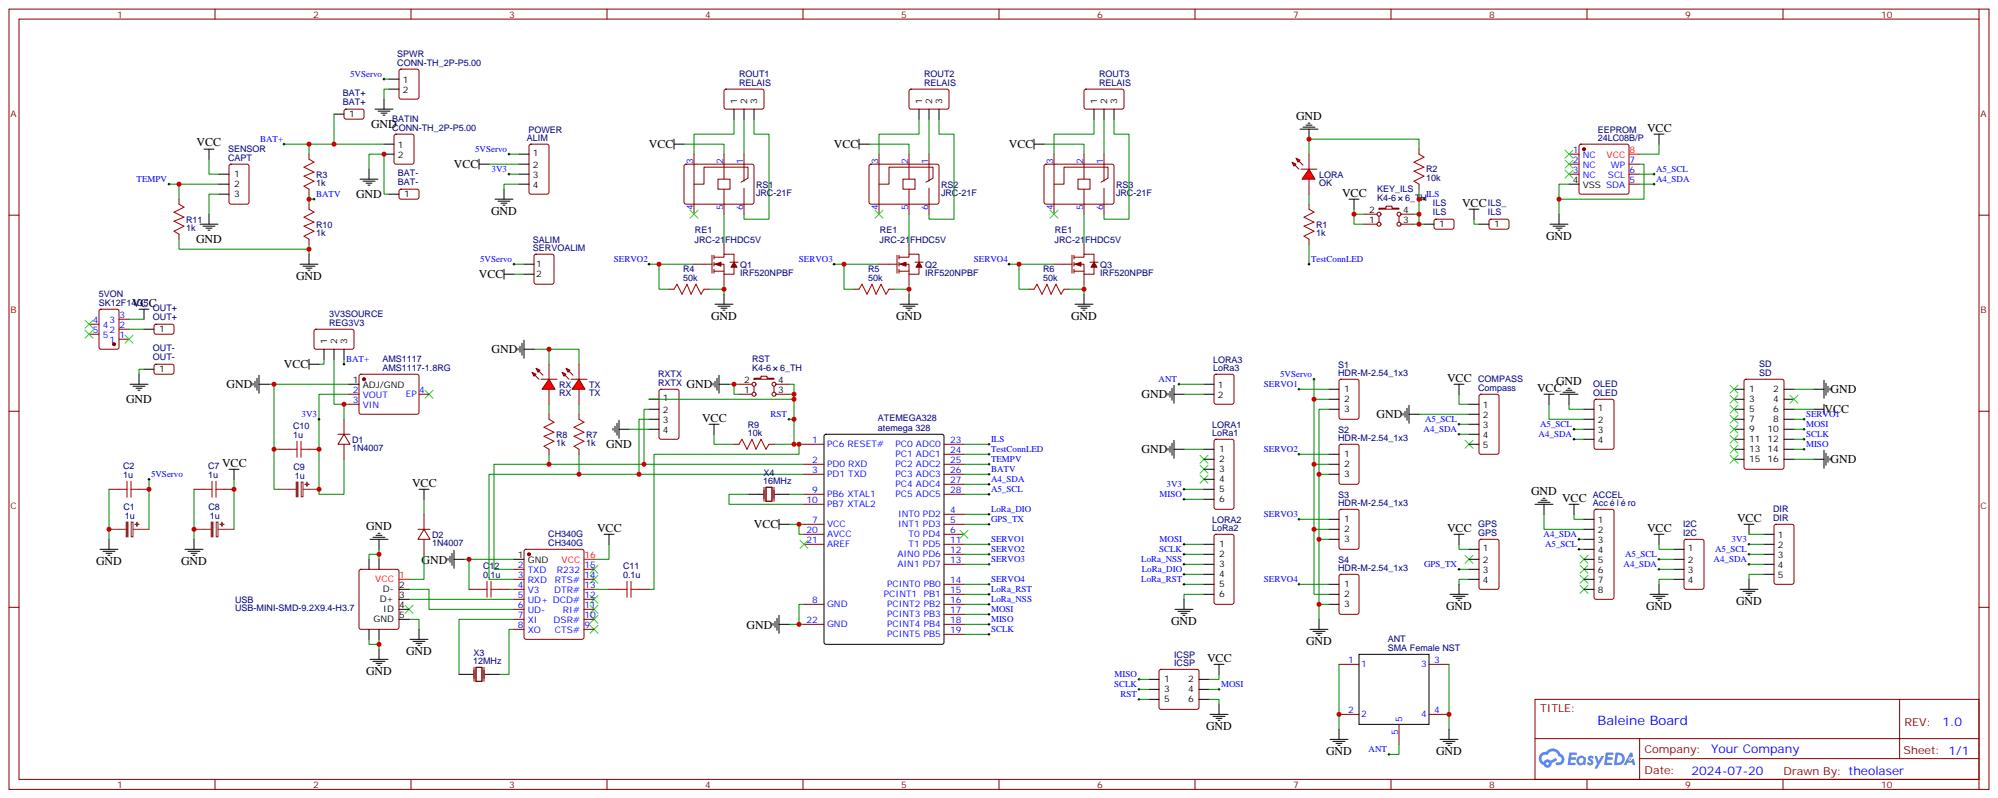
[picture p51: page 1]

DSR# 10 RI# 11 DCD# 12 DTR# 13 RTS# 14 R232 15 VCC 16

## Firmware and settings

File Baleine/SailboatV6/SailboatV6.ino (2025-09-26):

// Main code

#include "Abstraction.h"
#include "Navigation.h"
#include "Communication.h"
#include "Guidance.h"

void setup() {
  Serial.begin(9600);
  initAbstraction();
  initNavigation();
  initCommunication();
  initGuidance();
}

void loop() {

  /* Guidance loop */
  updateGuidance();

  /* Then, Abtraction loop */
  updateAbstraction();

  /* Communication loop */
  updateCommunication();

}

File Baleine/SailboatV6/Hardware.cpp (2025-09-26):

#include "Hardware.h"


TinyGPSPlus gps;
Servo rudder, sail;
MPU6050 mpu;
AS5600 windVane;
QMC5883LCompass compass;
sSoftSerial gps_serial(GPS_TX, GPS_RX);

/* I2C adresses :
compass 0x0D
accéléro 0x68
windvane 0x36
 */

GPSPoint lastUpdatedGPSPoint;
float GPSspeed;

void initHardware() {
  Wire.begin();
  Serial.println(F("SailboatOK"));
  pinMode(LED_PIN,OUTPUT);
  pinMode(KEY_PIN,INPUT);
  pinMode(A2,INPUT);
  pinMode(BATV_PIN, INPUT);
  /* Initialisation des objets */
  gps_serial.begin(GPS_BAUD);
  rudder.attach(DIR_PIN);
  sail.attach(SAIL_PIN);
  mpu.initialize();
  compass.init();
  compass.setADDR(0x0D);
  windVane.setDirection(AS5600_CLOCK_WISE);
  if (!windVane.isConnected())
    Serial.println(F("WindVaneFail"));
  compass.setSmoothing(5,true);
  //compass.setCalibrationOffsets(76.00, -358.00, -107.00);
  compass.setCalibrationOffsets(274.5, -487.00, -107.00);
  compass.setCalibrationScales(0.94, 1.12, 0.96);
  /* Initialisation des variables */
  GPSPoint lastUpdatedGPSPoint;
  lastUpdatedGPSPoint = {0, 0};
  GPSspeed = 0;
}

Attitude getAttitude() {
  int16_t ax, ay, az;
  mpu.getAcceleration(&ax, &ay, &az);
  Attitude att;
  att.roll = -atan2(-ax, az);
  att.pitch = -atan2(-ay*cos(att.roll), az);
  return att;
}

float getWindVaneAngle() {
  return 360 * ((float) windVane.readAngle() - WIND_VANE_MIN_VALUE) / (WIND_VANE_MAX_VALUE - WIND_VANE_MIN_VALUE);
}

Compass getCompass() {
  compass.read();
  return {compass.getX(), compass.getY(), compass.getZ()};
}

void lisenGPS() {
  while ((gps_serial.available() > 0)) {
    if (gps.encode(gps_serial.read())) {
      lastUpdatedGPSPoint.lat = gps.location.lat();
      lastUpdatedGPSPoint.lng = gps.location.lng();
      GPSspeed = gps.speed.kmph();
   }
  }
}

void updateHardware() {
  lisenGPS();
}

float getVoltage() {
  return 7.7932*analogRead(BATV_PIN)/279.0;
}

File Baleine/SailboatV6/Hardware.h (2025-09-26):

#include <Servo.h>
#include <MPU6050.h>
#include <QMC5883LCompass.h>
#include <TinyGPSPlus.h>
#include "sSoftSerial.h"
#include "Utils.h"
#include "Arduino.h"
#include <AS5600.h>

/* Define pinout */
#define LED_PIN A1
#define BATV_PIN A3
#define KEY_PIN A0
#define DIR_PIN 7 // 7
#define SAIL_PIN 8 // 8
#define GPS_TX 3
#define GPS_RX 4

#define GPS_BAUD 9600

#define WIND_VANE_MIN_VALUE 0.0
#define WIND_VANE_MAX_VALUE 4095.0


extern Servo rudder, sail;
extern GPSPoint lastUpdatedGPSPoint;
extern float GPSspeed;

#ifndef ATTITUDE_STRUCT
#define ATTITUDE_STRUCT
struct Attitude {
  float roll;
  float pitch;
};
#endif

void initHardware();

void updateHardware();

float getWindVaneAngle();

Attitude getAttitude();

Compass getCompass();

float getVoltage();

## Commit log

2025-09-26 add cfd files
    [HullUDF.obj, HullUDFV2.obj, udf_names.obj]
2025-09-26 add cfd drift
    [Airfoil.SLDPRT, BulbForceCOMSOL.csv, BulbTorqueCOMSOL.csv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]
2025-09-26 add posidonie files
    [ExpérienceCornière.xlsx, HullV5.STL, RowingBoat.stl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]
